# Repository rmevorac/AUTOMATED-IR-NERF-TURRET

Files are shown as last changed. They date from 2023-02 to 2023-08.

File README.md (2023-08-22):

# AUTOMATED IR NERF TURRET MECHA 20
# ME 405 Term Project

### by: Ben Elkayam, Ermias Yemane, Roey Mevorach

## Introduction
This projects goal was to design, construct and program a automated nerf turret that is capable of shooting a person 16 feet awya using an IR camera for signal detection. The firing conditions for this turret are a predetermined set of "dueling rules" specified in the following steps:

1. The turret must start facing away from the intended target
2. The turret will then roate 180 degrees to face the general area of the intended target
3. The intended target will have 5 seconds to move around. by this point your turret is allowed to fire.
4. After 5 seconds from the start of the duel the intended target must stand still for atleast 10 seconds.
5. The turret can fire any amount of shot sduring either step 3 or 4. The scoring is based on if the opposing targets turret hit first, how many shots hit, and how many shots missed. 

The turret is intended to be used exclusivley for the ME 405 Learn by Dueling Competition by the students who designed and programmed it and another other ME 405 students who wanted to try using the turret. 

---

# Turret Design

## Hardware Design
Our hardware design philisophy is based almost entirley around being compatible with the NERF gun we chose. For our turret we chose the NERF Ultra Select 2. An electronic firing mechanism and flywheel firing system where desirable as it made actuating the gun a pre-packaged operation. The only difficulty was the size of the gun made it difficult to design a fixture for. The design is outlined in [our CAD folder](https://github.com/rmevorac/ME-405-term-project/tree/main/SLDWRK). The 3 important design attributes of our final turret design are the yaw axis, the pitch axis, and the fixture. The yaw axis is composed of a lazy susan that sits on 4 legs conencting to the bottom half, and a pivot with a shaft coming through the middle of bearing downards which sits on the top. The yaw axis is driven by the 405 kot motors through a 400mm belt and a 3.75:1 torque pulley ratio. The pivot which composes the pitch axis as was designed around a set of 30mm bearing found within the ME 405 lab. The pivot piece which the large black 3D printed object, was printed with the assistance and guidance of Thomas Mcklay Taylor, another ME 405 student. The pitch axis is driven by a worm gear to spline gear system with an approximate gear ratio of 11:1 as to not be easily backdrivable. This drives a winch system that raises and lowers the gun. The pivot is attached to the final component set which is known as the gun clamp. This is a two piece mechanism which both acts as the shaft for which the gun pivots around and the mechanism which keeps the gun secured to the turret. Photos of the general design are provided below:

### General View:
<div align='center'>
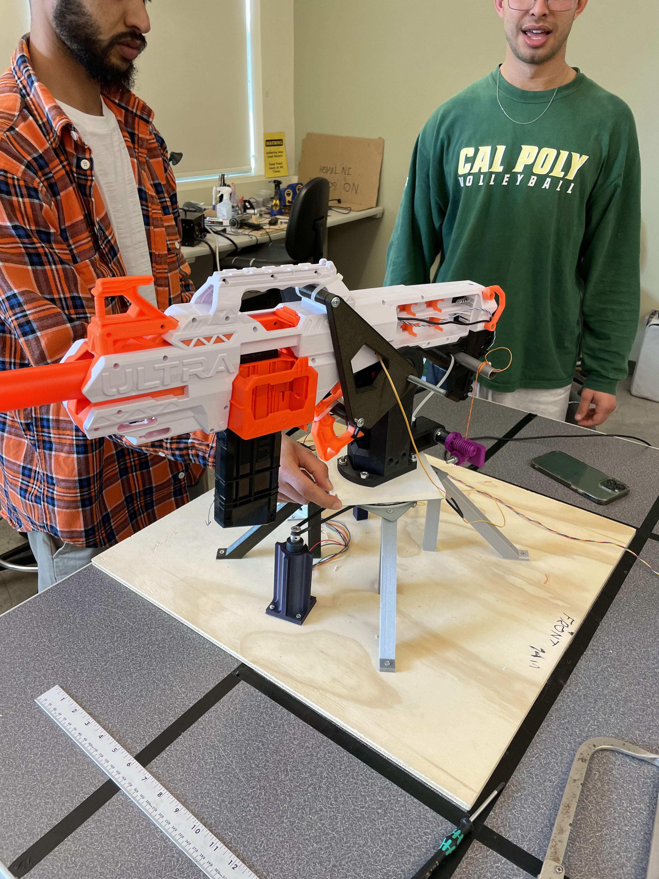
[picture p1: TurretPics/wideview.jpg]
wide view

</div>

### Yaw Axis:
<div align='center'>
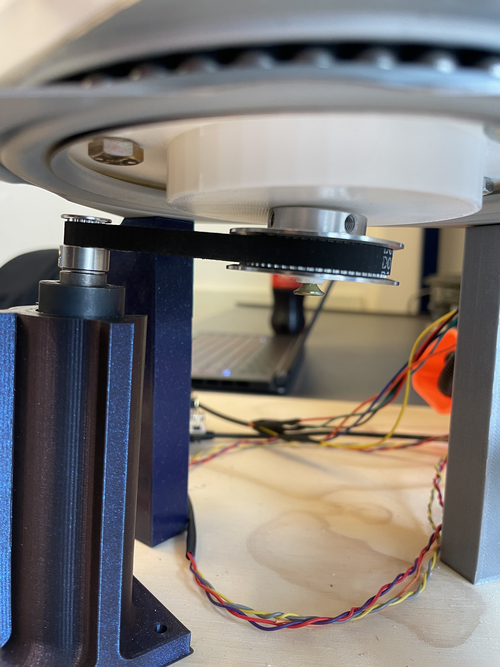
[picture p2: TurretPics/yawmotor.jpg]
yaw

</div>

### Pitch Axis:
<div align='center'>
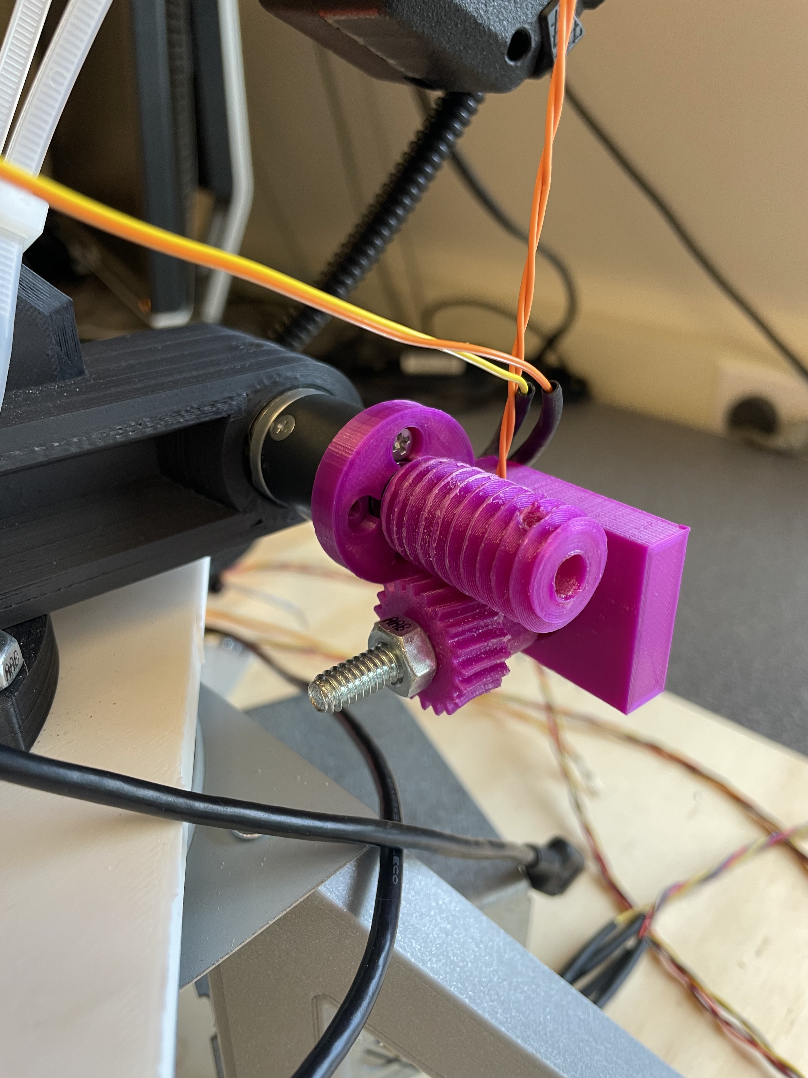
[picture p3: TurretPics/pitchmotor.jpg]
pitch

</div>

### Gun Pivot:
<div align='center'>
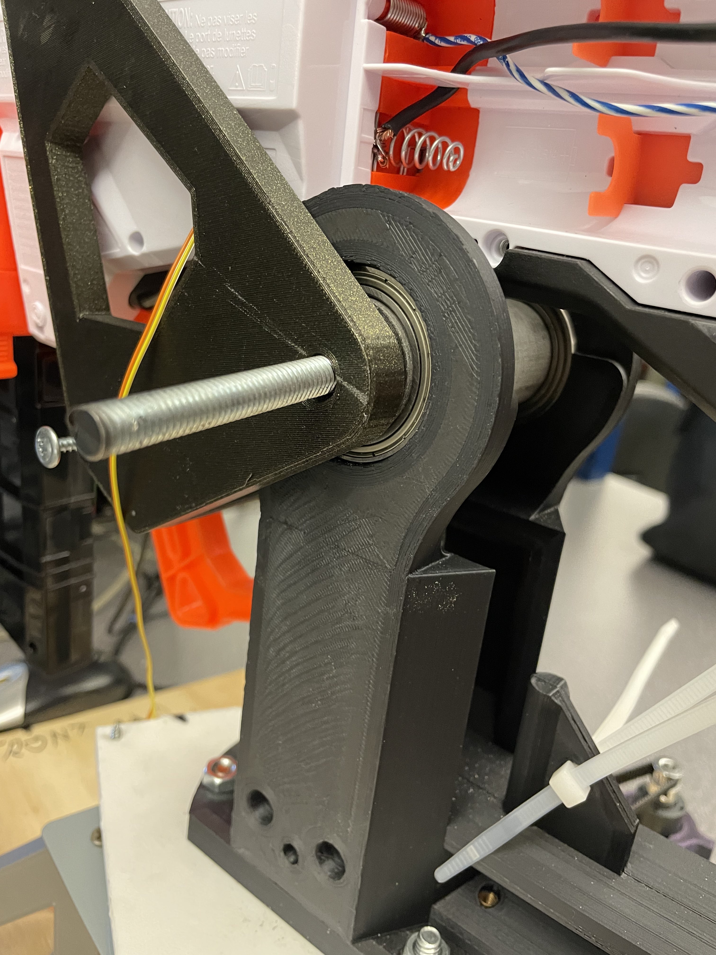
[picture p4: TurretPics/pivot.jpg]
pivot

</div>

### Firing Access Modification:
<div align='center'>
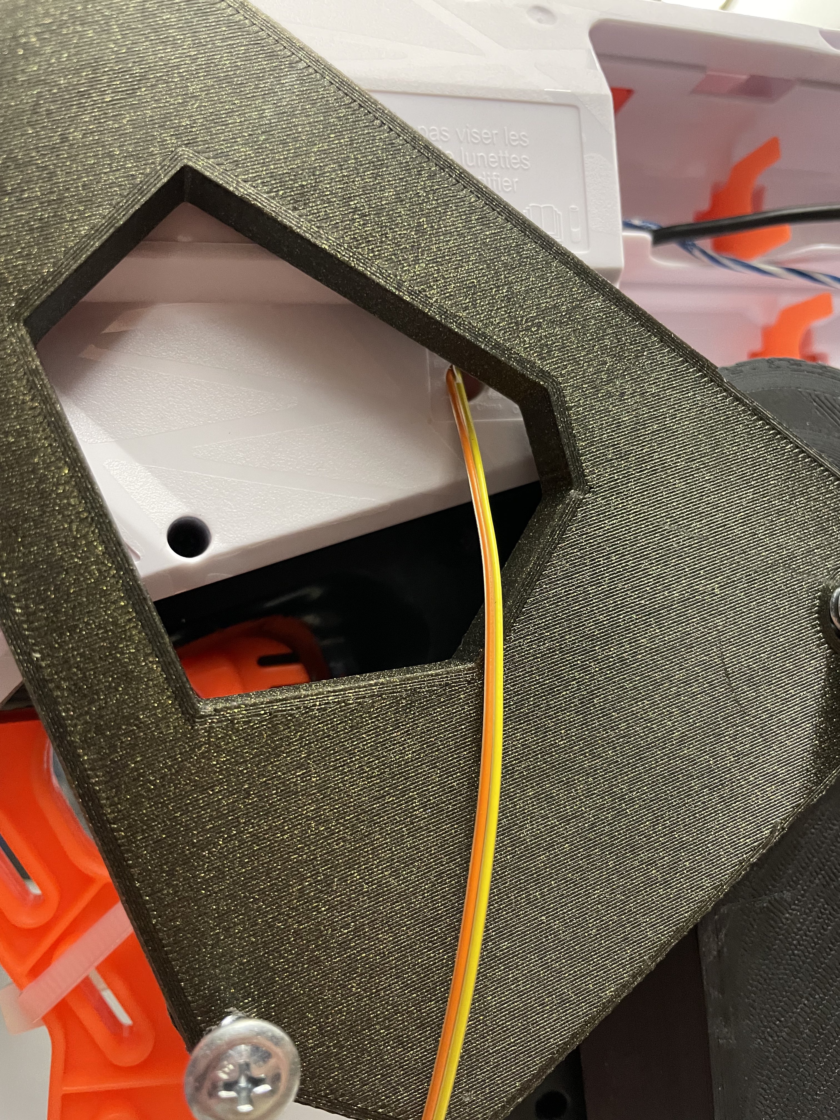
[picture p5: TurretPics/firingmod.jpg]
fireaccess

</div>

### Electronic Design
In terms of electronic design, the modifications made to the gun is directly replacing the firing signal from a button within the NERF gun with a set of wires to allow external control of the firing mechanism. The second change was to soder longer power cables to the battery touchpoints in order to have the turret be able to be connected to the power supplies. A secondary part of our electronic design is that we ziptied the flywheel trigger down rather than seek a direct electrical control solution because we realized we would always want the flywheels on.

## Software Design
Our software design is based on a cooperative multitasking design around 4 tasks. These tasks are our pitch motor, yaw motor, target acquisition, and firing mechanism.

Our code implements a cooperative multitasking scheduler using the cotask and task_share modules. Tasks are defined as functions, and they yield control back to the scheduler using the yield statement. The scheduler then runs the next task until it yields or completes. Shared data between tasks is managed using shared variables provided by the task_share module. Overall, the code is running several tasks concurrently and using shared variables to communicate between them, allowing for cooperative multitasking.

Our main program defines four tasks, two of which control the movement of the pitch and yaw motors. The program begins once the user button on the microcontroller is pressed. The system then begins its first task, which turns the gun around by 180 degrees. The system then waits for 5 seconds and moves to the next task. The next task uses the image produced by the IR camera to obtain the coordinates of the target (hottest pixel). These coordinates are then converted to ticks using simple geometry and other calculations, and are set as the motors' new setpoints. The motors then run until they reach the range of that setpoint. Once both motors are in position,
the final task is triggered, which fires the NERF gun.

Our Finite State diagrams and Task diagram are provided both here and in our doxygen. Our software design is provided in great detail on our doxygen gituhub.io page for this project, please refer to the link below for more detailed information: https://rmevorac.github.io/AUTOMATED-IR-NERF-TURRET/index.html

### Task Diagram:
<div align='center'>
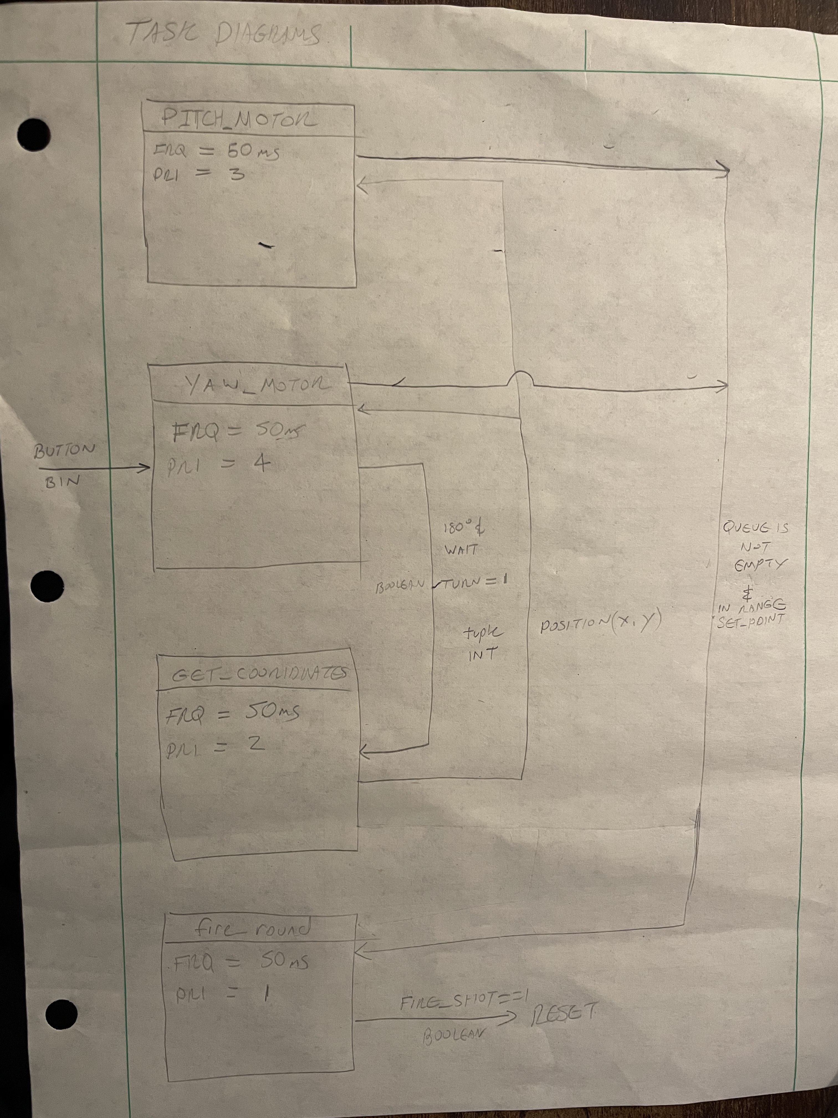
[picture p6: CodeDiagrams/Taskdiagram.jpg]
task

</div>

### Finite State Diagrams:
<div align='center'>
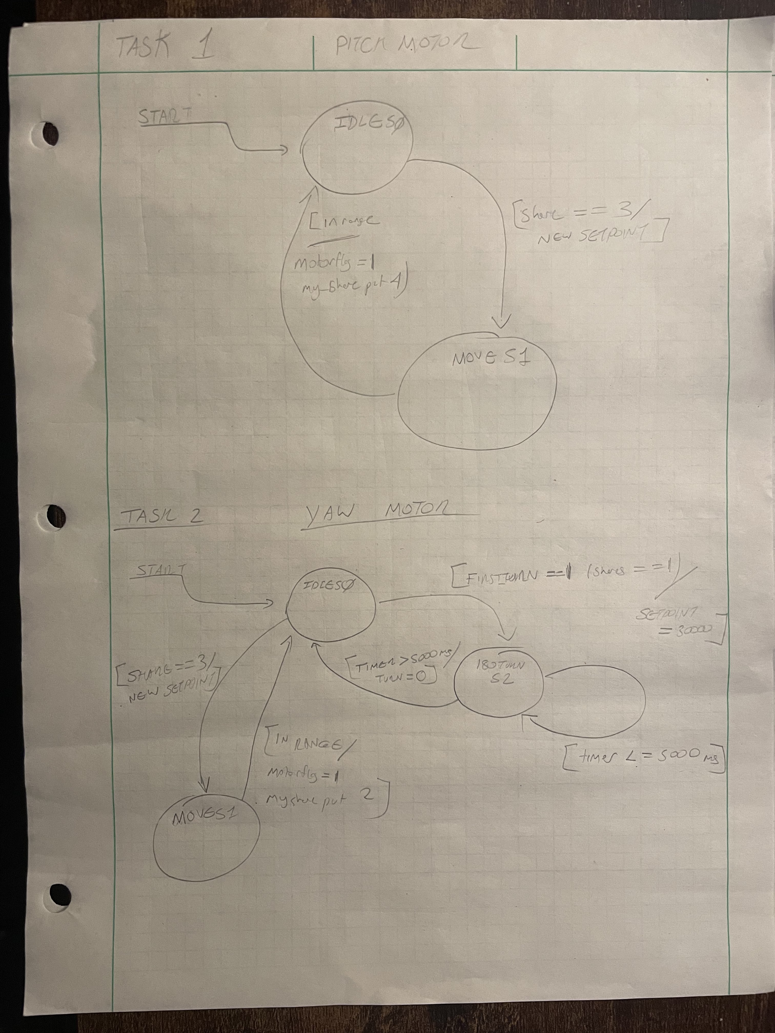
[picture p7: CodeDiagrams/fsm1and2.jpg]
fsm1and2
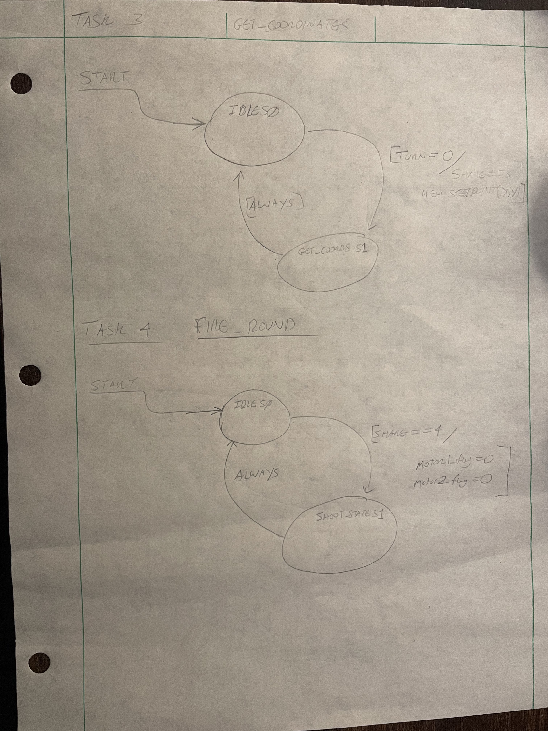
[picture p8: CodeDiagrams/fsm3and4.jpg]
fsm3and4
 
</div>

---

# Project Outcome

## Duel Day Performance
Our turret reach ours sections finals, but in a dissapointing way. Its tracking was excellent and was able to easily follow the target, however a mysterious code gremlin popped into our design sometime during the 3 hous between the end of our all-nighter the night before and our designated dueling time. While we lost no points, we gain none either as we could noot shoot. No amount of good tracking will fix a gun that doesnt shoot. We are unsure why it worked the night before then refused to work during the duel and did attempt to discover why during the friday after the duels. We eventually determined that the issue was a mixture of too much current draw and a strange calibration issue with our on/saftey stop button code. Ultimatley, we where proud of how our gun functioned while it worked and regret it could not operate at is best during the dueling day.

### Testing Results
We tested similarly to how we would duel, the onlly difference is that the test subject did not have their own turret at the end of the table. We decided to test like this because we wanted to calibrate the turrets accuracy to the same conditions the duel would take palce in. during the calibration testing the night before, the turret was opperating very effectivley and was landing 5 hits for every 8 shots. We anticiapted a good performance on duel day assuming the turret would function the same. 

## What We Learned
There was many things learned through this project and should be categorized into Mechanical, Eletrical and Software lessons. The brief summary for anyone attempting this project can be seen below in the Dos and Donts:

### Dos:
1.Use an eletrical firing system. Eletrical nerfguns are simply easier to actuate and shoot very effecitlvey. The pre-packaged design makes them easy to integrate into a turret.

2.Supply power through a power supply rather than batteries, we are grateful that it reduced the weight of our gun and during its functional peroid it gave us very consistent firing results.

3.Keep the tracking algorithim simple, we observed many people doing complex manipulation of the thermal array and have reduced accruacy than ours, just reading from the array keeps the processing light and provides highly reliable tracking.

4.Consider non-backdrivable systems. While the high gear ratio lsows down your turning, we removed alot of backlash in our axis that had our worm-spline gear system

5.We added a physical hardstop on our guns base to help us zero the gun for every duel. 

### Donts:
1. Do not rely on only 3D pritned components due to the fragility of them as tensile load bearing structures. Consider including wooden or metal components for this such as shafts.
2. Ensure that any custom eletric circuit system is as compatible as possible with the electronics within your NERF Gun as a lack of compatibility will cause misfires.
3. Conduct thorough tests to ensure new code does not inhibit core functions and prioritize that rather than calibration testing. 

### Mechanical Lessons
Most of our hardships where due to the heavy use of 3D printed parts. We originally designed our system to have pulleys fixed onto 3D printed shafts, however we soon realized why thats a problem. All our parts where experencing stress perpendicular to the plane of printing which caused layer seperation and broke our shafts and bearing mounts off. This was remedied in two ways. The layer seperation on our bearing mounts was fixed with the help of Thomas Taylor who advised on a printing strategy that would change the direction of the print layer and increase strucutral rigidity through brass inserts. We are very grateful for his assistance concerning this part and his advice has helped all of us become more competent designers for 3D printing. For the shafts, thier snapping was remedied differently depending on the axis. For the yaw shaft, a generous amount of plastic bonder cement was applied with the snapped shaft and pulley to the original base. For the pitch shaft, the system was replaced with the worm gear-spline gear winch mechanism which opperated with much less backlash than the original pulley system. Overall the lesson here is do not trust 3D printing on its own for structural applications, it should be combined with additional components and be put in compression rather than tensile loads.

### Eletrical Lessons
The eletrical side of our turret seemed to work fine up until our last moments, wherein we suspect it to possibly be part of our firing issue. The turret's firing mechanism is a simple circuit with the two firing wires sending a shoot signal when shorted. To protect the STM output pins, we implemented a BJT-transistor switch which was used to open and close the connection. This was the extent of the circuit we had, which leads us to believe that we possibly needed to investigate our eletrical circuit much more thoroughly to ensure we would not have misfires as one of our members believes that current leakage may of been our issue or that our microcontroller could not provide enough current because the gate capacitance was too large.

### Software Lessons

Our software side learning was the most mild as all the previous tools such as our motor controller and camera components where easy to implement. We decided to go with a simple but effective scanning method with our camera wherein we simply checked every cell and its neighbors. The cell with the highest combined value of itself and its neighbors had its row and column stored and we did that for the entire thermal camera array. This system provided us good tracking results after some calibration. Our biggest coding hump was trying to implement a system that allowed us to use the blue user button on the microcontroller to start and stop the turret. We first where having issues with our ExtInt system throwing errors which was due to improper naming conventions within our code and then had trouble implmenting it into our code. We ended up putting each of our tasks in a while loop that depended on the button's boolean being set in order to function, this gave use essentially a pause button functionality on our turret.

---

# Original Description and additional files

We are intending to make a 2 axis turret equipped with an electronic nerf launcher. The goal is to use a medium sized motor likely one of the tub motors for horizontal panning and either a more powerful motor we purchased online or a dual tub motor gearbox. We are likely going to 3D print most of the superstructural pieces and manufacture components like the trigger mechanism. The goal is to get the gun to land the first shot. We are confident on our electric gun choice but unsure on the motor selection.

Motors: 
Pitch Motor : Tub motor 
Yaw Motor: 1 – 2 Tub motors

Drive System: 
Pitch: Likely a single gear step (not including gearbox on motors) in the range of 2:1 to 4:1
Yaw: Also a single gear step in the range of 2:1 to 5:1 or utilize a two motor gearbox

Nerf Gun:
Vendor: Amazon
Model: Nerf Ultra Select
https://www.amazon.com/NERF-F0958-NER-Ultra-Select/dp/B08SYD2685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

Data sheet for Nerf Gun: https://icecat.biz/p/nerf/f0958u50/ultra-toy+weapons-5010993855285-select-89523906.html

Data sheet for Adafruit MLX90640 IR Thermal Camera: https://learn.adafruit.com/adafruit-mlx90640-ir-thermal-camera/downloads

Trigger System:
Electronic Trigger System

Total Cost:
Nerf Ultra Select Gun - $51

Task Diagram:
<div align='center'>
TDV1
</div>

FSM:
<div align='center'>
FSMV1
</div>

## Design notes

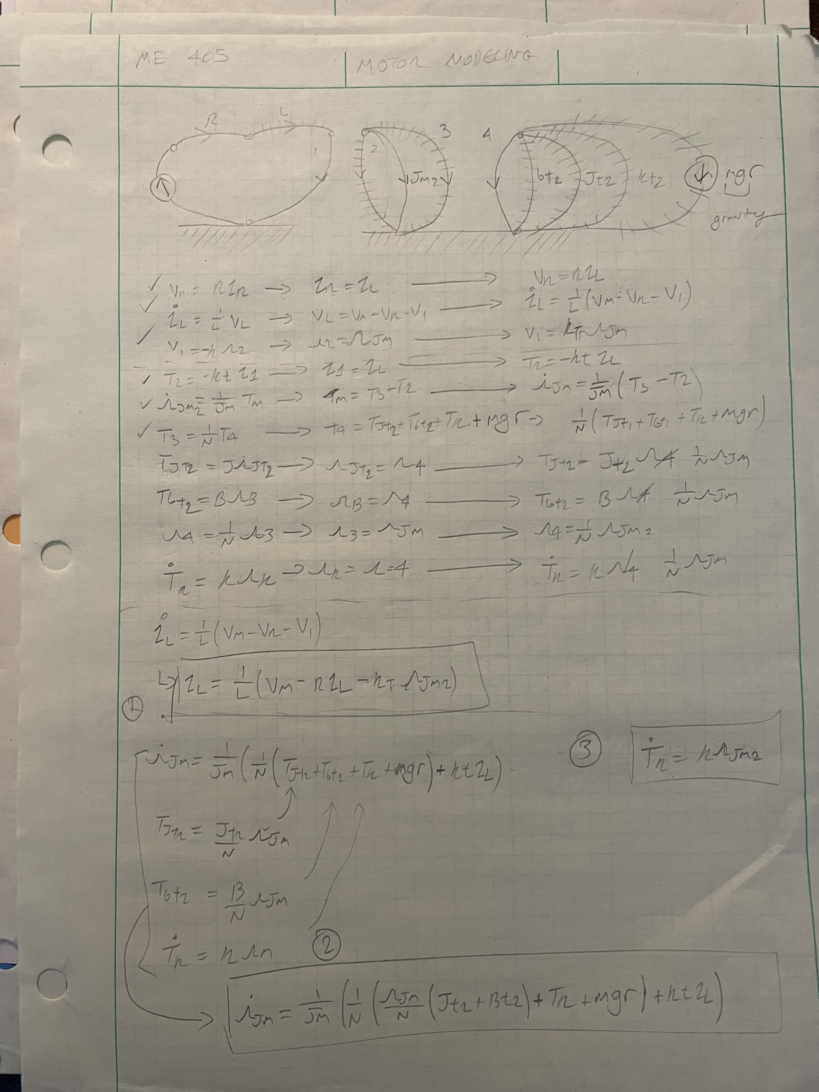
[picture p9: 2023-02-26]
spec_docs/equations/motor2_img1.jpg

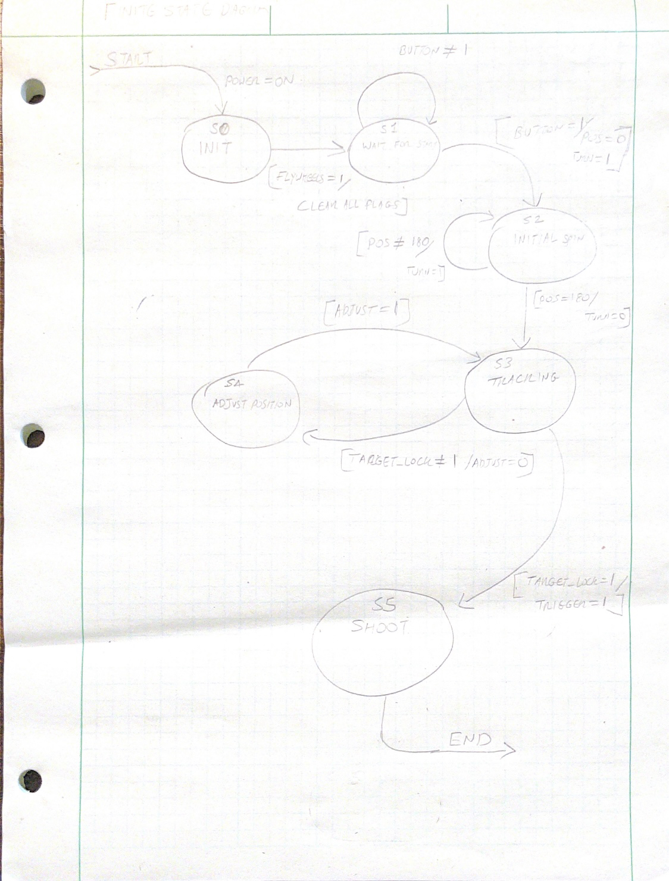
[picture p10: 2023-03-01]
spec_docs/FSMV1.jpg

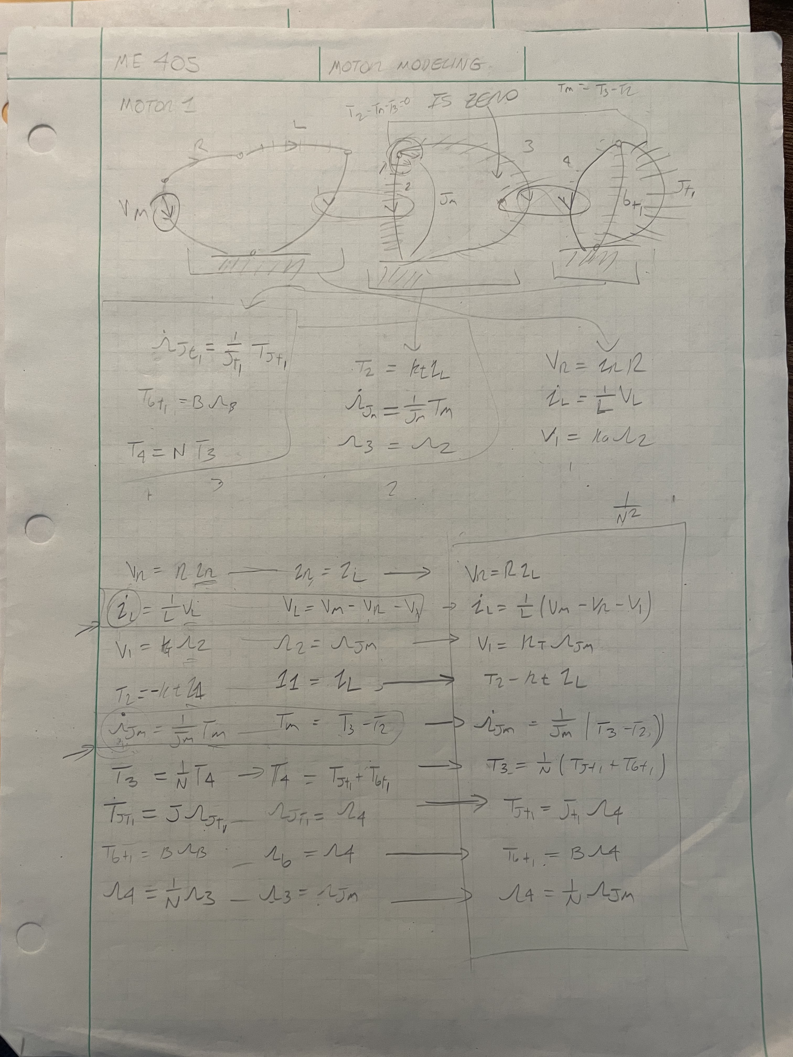
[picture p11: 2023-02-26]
spec_docs/equations/motor1_img1.jpg

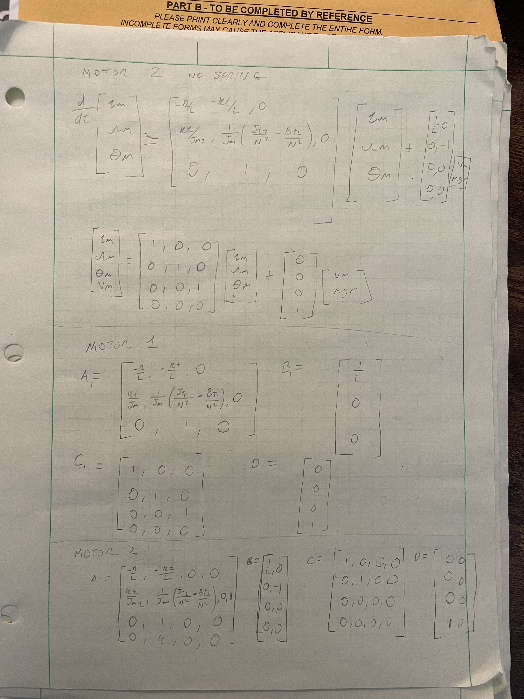
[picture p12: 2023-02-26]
spec_docs/equations/matrices_without_spring.jpg

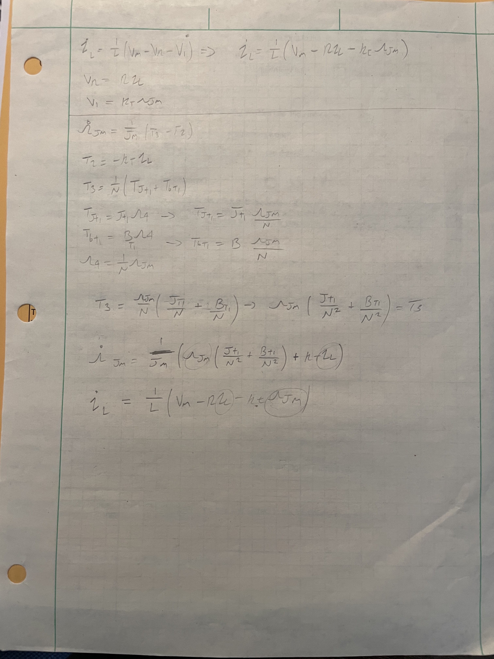
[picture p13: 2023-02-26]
spec_docs/equations/motor1_img2.jpg

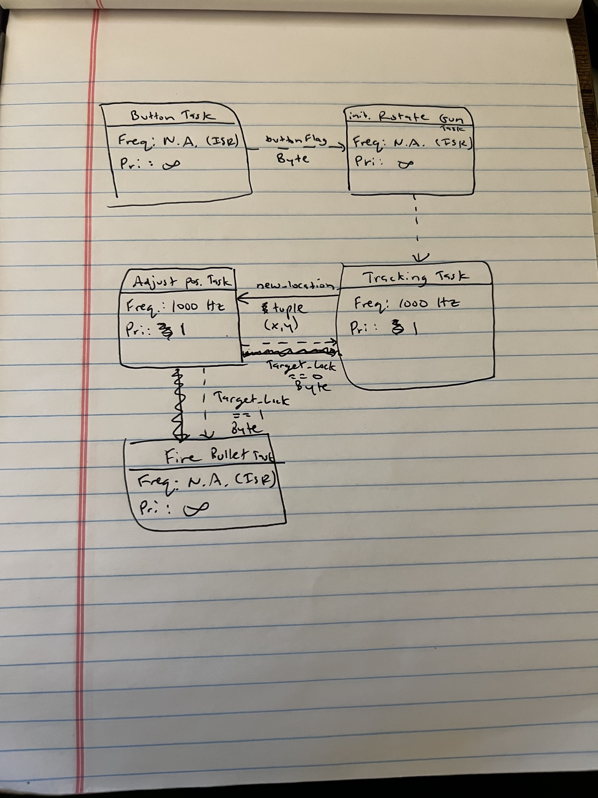
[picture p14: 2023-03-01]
spec_docs/TDV1.jpg

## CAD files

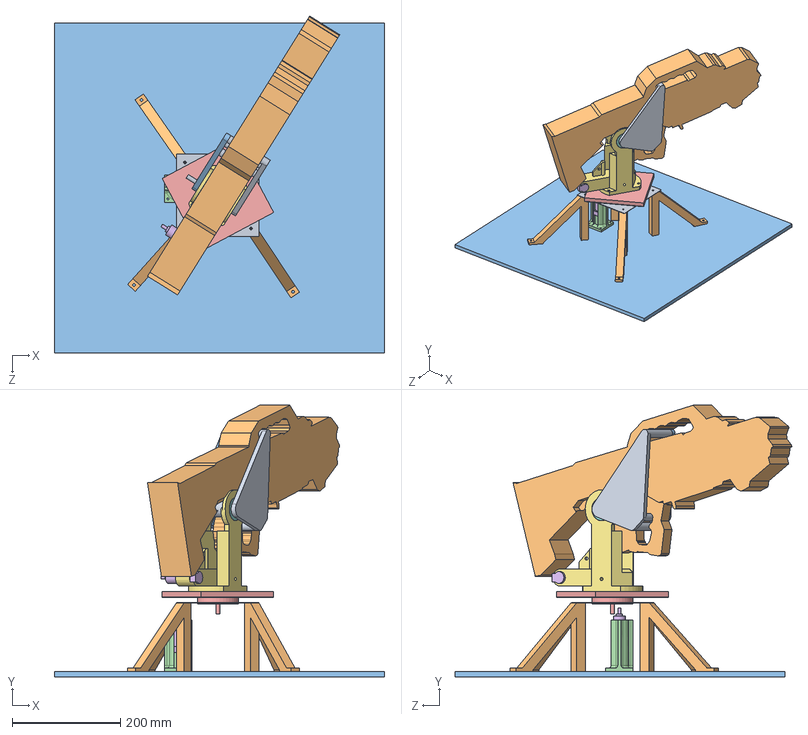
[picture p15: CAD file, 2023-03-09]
SLDWRK/Mainassemb.SLDASM
609.6 x 501.6 x 622.5 mm
LSB
base legs x 4
baseboard
LST
3d topbase
verticalframe
bearings x 2
clamp1
gun
clamp2
motormountyaw

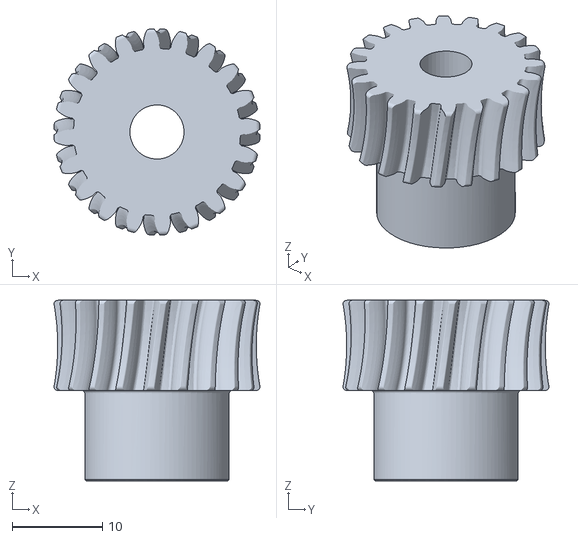
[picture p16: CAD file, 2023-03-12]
SLDWRK/Part1.STL
22.8 x 22.8 x 20.0

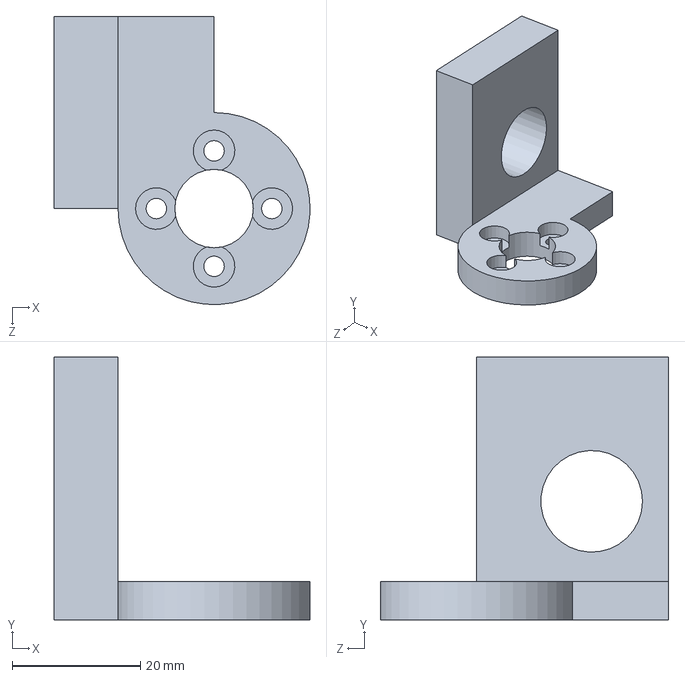
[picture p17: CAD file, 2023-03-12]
SLDWRK/winchmount.SLDPRT
40.0 x 41.0 x 45.0 mm

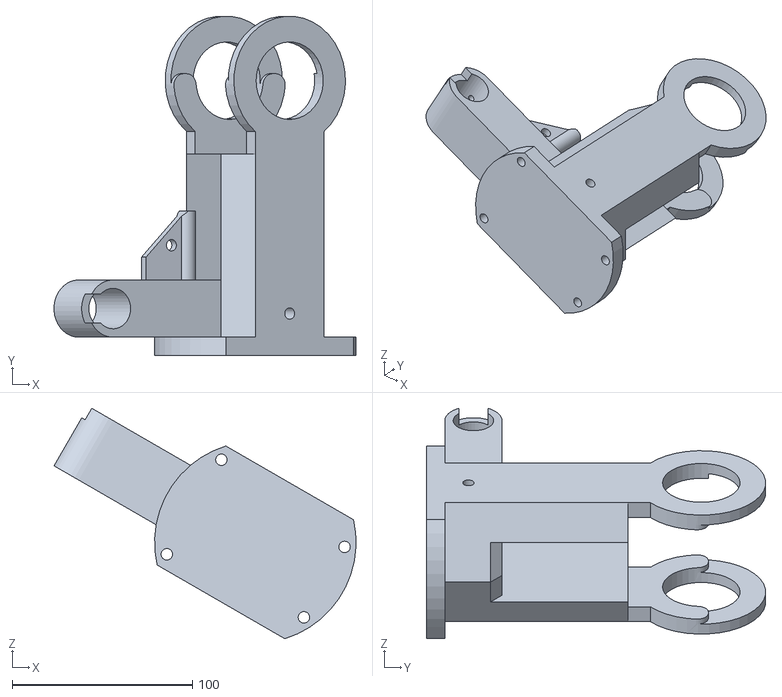
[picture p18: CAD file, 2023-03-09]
SLDWRK/verticalframeversion2.STL
167.5 x 188.0 x 127.8

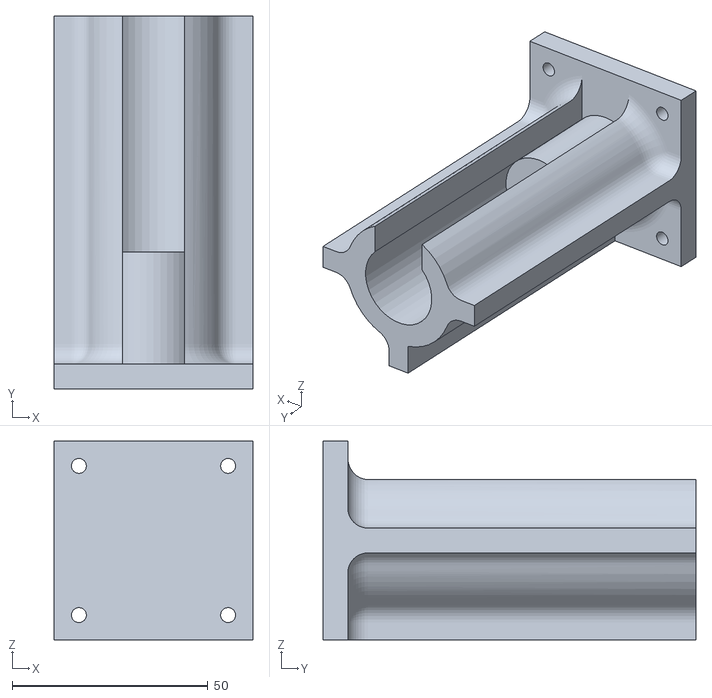
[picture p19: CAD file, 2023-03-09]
SLDWRK/motormountyaw.STL
50.8 x 95.2 x 50.8

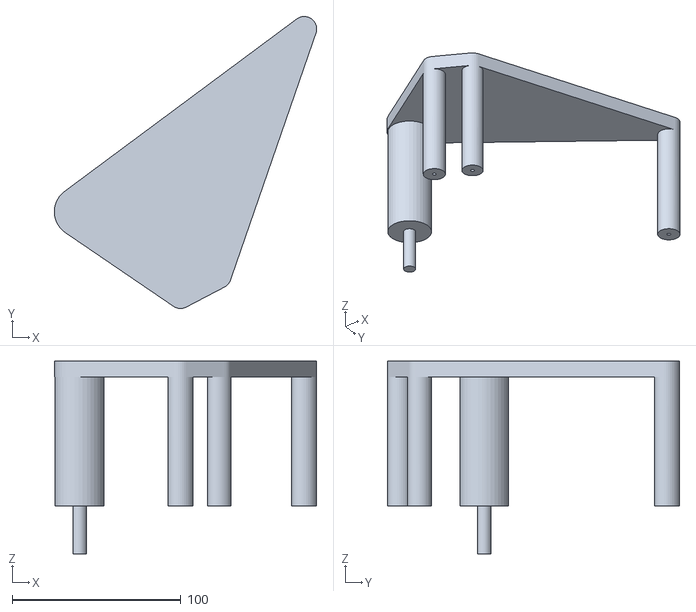
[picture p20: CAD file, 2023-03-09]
SLDWRK/clamp1.STL
155.6 x 173.1 x 114.4

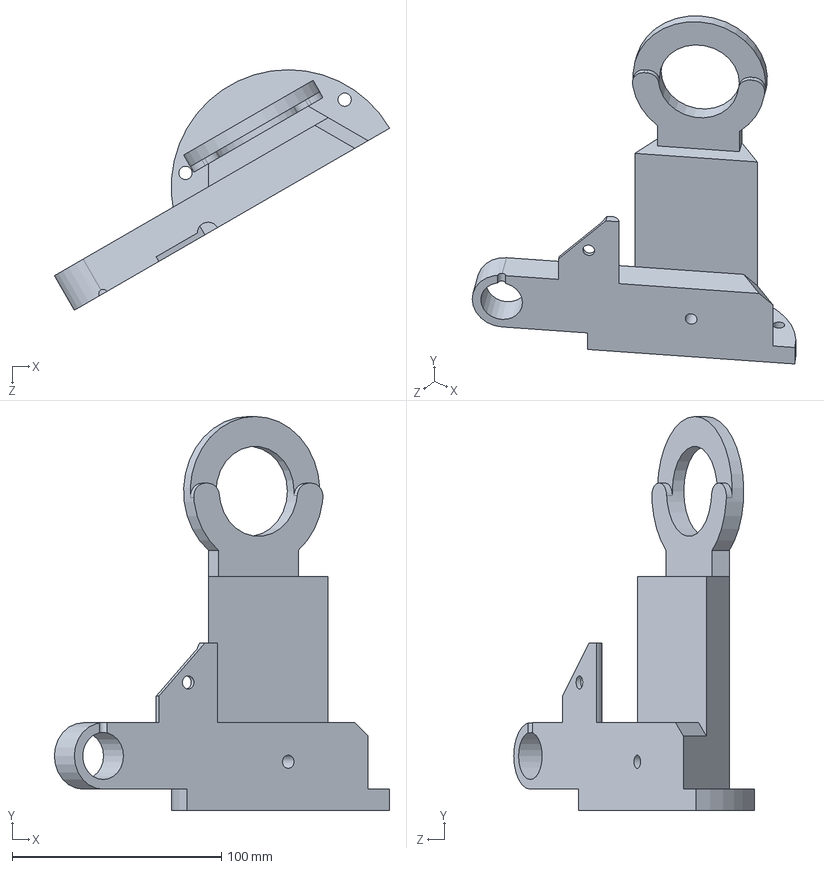
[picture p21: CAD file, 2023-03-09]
SLDWRK/verticalframesplit1.SLDPRT
160.1 x 188.1 x 114.9 mm

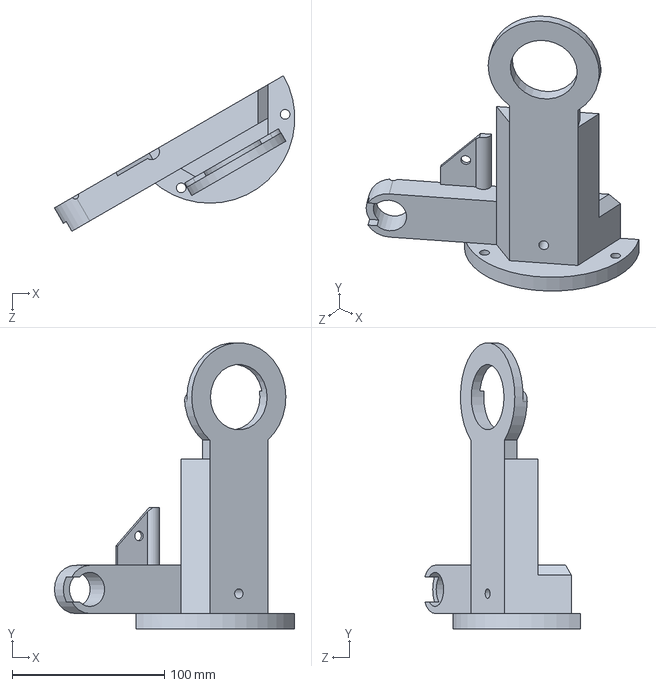
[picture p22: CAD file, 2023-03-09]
SLDWRK/verticalframesplit2.SLDPRT
157.9 x 188.0 x 102.3 mm

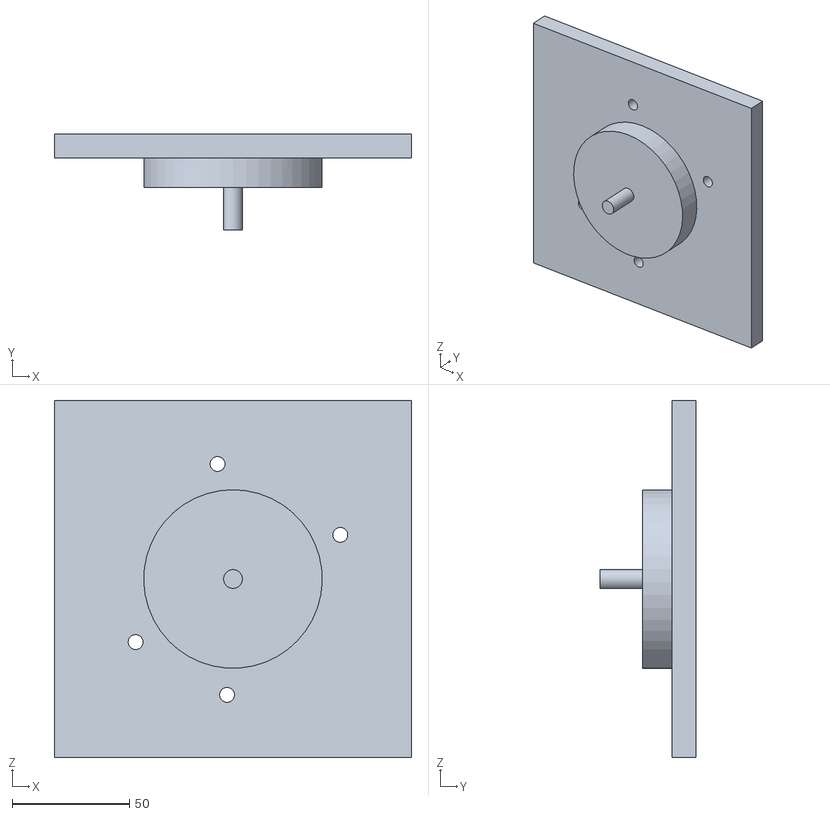
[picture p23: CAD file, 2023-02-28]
SLDWRK/3d topbaseV2.STL
152.4 x 40.9 x 152.4

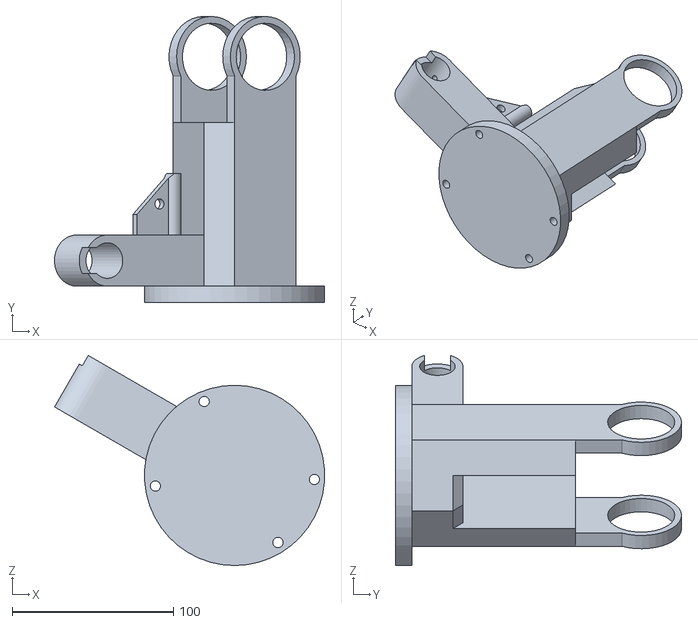
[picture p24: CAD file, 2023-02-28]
SLDWRK/verticalframeSTRUCTURE.STL
167.4 x 177.4 x 130.2

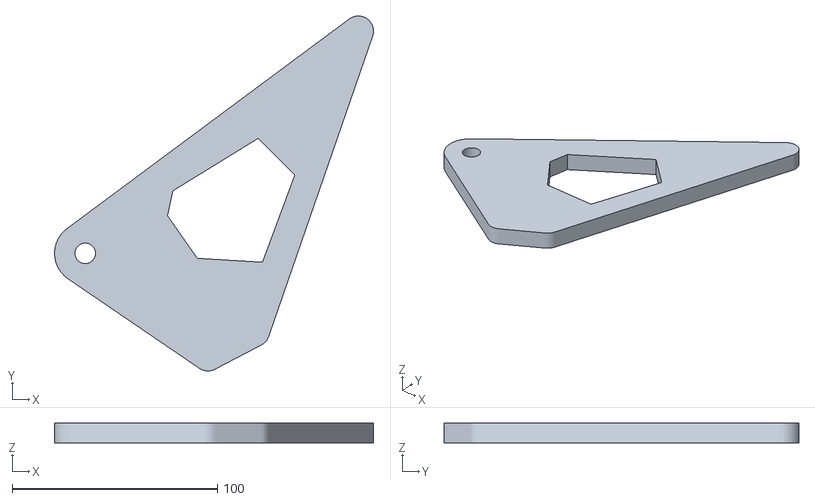
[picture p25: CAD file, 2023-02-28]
SLDWRK/clamp2.STL
155.6 x 173.1 x 9.53

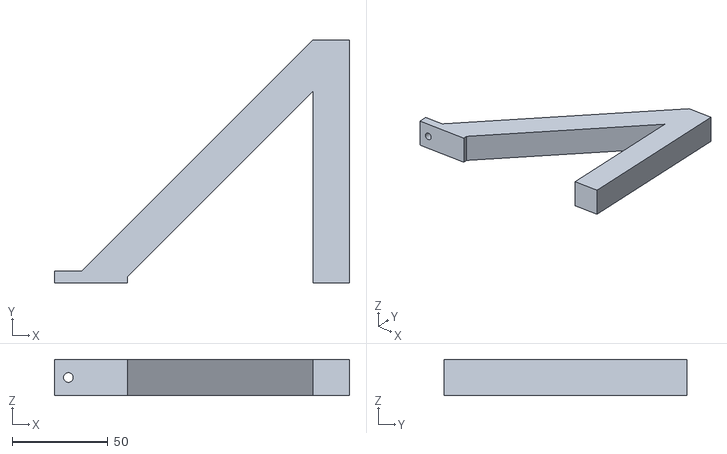
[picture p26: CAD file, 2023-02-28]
SLDWRK/base legs.STL
154.0 x 127.0 x 19.1

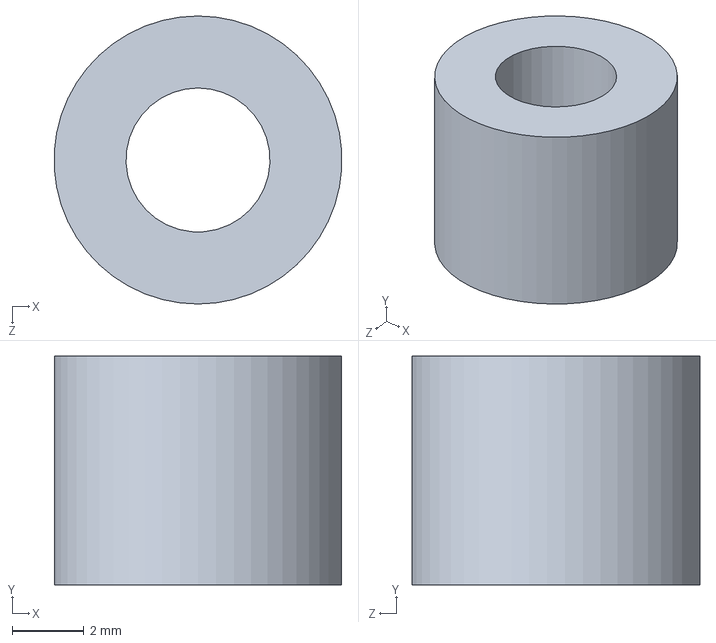
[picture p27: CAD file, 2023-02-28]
SLDWRK/8to6shim.SLDPRT
7.98 x 6.35 x 8.00 mm

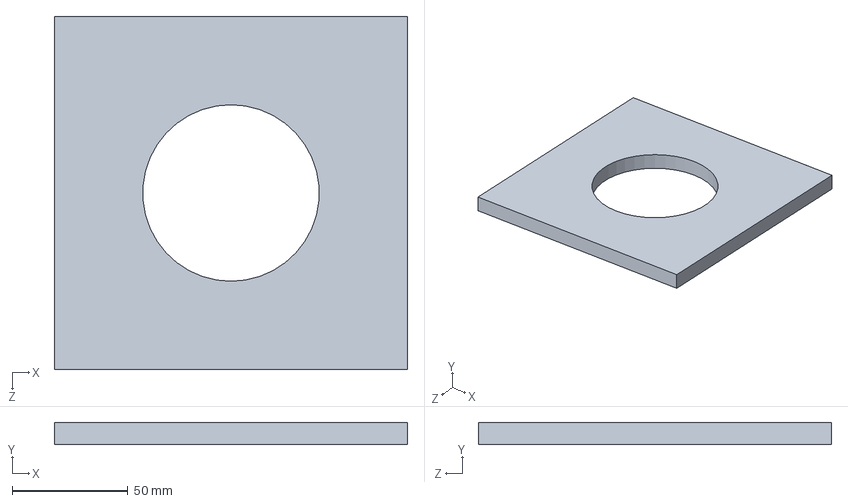
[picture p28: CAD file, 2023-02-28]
SLDWRK/plywood topbase.SLDPRT
152.4 x 9.53 x 152.4 mm

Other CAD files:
SLDWRK/3d topbase.SLDPRT
SLDWRK/57545K764_Metal Worm Gear.SLDPRT
SLDWRK/57545K633_Steel Worm.SLDPRT
SLDWRK/3d topbase.STL
SLDWRK/57545K633_Steel Worm.STL
SLDWRK/57545K764_Metal Worm Gear.STL
SLDWRK/verticalframesplit1.STL
SLDWRK/verticalframesplit2.STL
SLDWRK/winchmount.STL

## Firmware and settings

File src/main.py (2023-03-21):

"""!
@file main.py
    This code is for a control system that moves a NERF gun to a specific set of angles using
    two motors: a pitch and yaw motor. The system includes a IR camera (MLX90640), which produces
    an image to obtain the coordinates of the target. The system is activated/paused by pressing
    the user button on the microcontroller.

    This program implements a cooperative multitasking scheduler using the cotask and task_share modules.
    Tasks are defined as functions, and they yield control back to the scheduler using the yield statement.
    The scheduler then runs the next task until it yields or completes. Shared data between tasks is
    managed using shared variables provided by the task_share module. Overall, the code is running several
    tasks concurrently and using shared variables to communicate between them, allowing for cooperative multitasking.

    This program defines four tasks, two of which control the movement of the pitch and yaw motors. The program
    begins once the user button on the microcontroller is pressed. The system then begins its first task, which
    turns the gun around by 180 degrees. The system then waits for 5 seconds and moves to the next task. The next task
    uses the image produced by the IR camera to obtain the coordinates of the target (hottest pixel). These
    coordinates are then converted to ticks using simple geometry and other calculations, and are set as the motors'
    new setpoints. The motors then run until they reach the range of that setpoint. Once both motors are in position,
    the final task is triggered, which fires the NERF gun.


@author Ben Elkayam
@author Roey Mevorach
@author Ermias Yemane

@date   2023-Mar-20
"""
"""!
@package pyb                Contains all micro controller tools we use.
@package gc                 Contains a garbage collector tool.
@package utime              Contains functions for getting the current time and date, measuring
                            time intervals, and for delays.
@package machine            Contains specific functions related to the hardware on a particular board.
@package math               Contains mathematical functions.

@package cotask             Contains the class to run cooperatively scheduled tasks in amultitasking system.
@package task_share         Contains the class that allows tasks to share data without the risk
                            of data corruption by interrupts.
@package encoder_reader     Contains our encoder driver class and data.
@package motor_driver       Contains our motor driver class that interfaces with the encoder.
@package controller         Contains our controller class which combines the motor and encode classes.
@package mlx_cam            Contains a wrapper class for accessing and using the IR camera (MLX90640)
"""
import pyb
import gc
import utime as time
from machine import Pin, I2C
from math import atan, pi

import task.cotask as cotask
import task.task_share as task_share
from motor.encoder_reader import Encoder
from motor.motor_driver import MotorDriver
from motor.controller import Controller
from mlx90640.mlx_cam import MLX_Cam

NUM_PIXELS_COL = 32
NUM_PIXELS_ROW = 24

def button_press(pin):
    """!
    @brief      This is the callback function that is called when the interrupt
                is triggered when the user button is pressed
    @details    This function is called when the user button on the microcontroller
                is pressed. The global variable button_count starts at 0. It is then
                incremented to 1 when the button is pressed for the first time, allowing
                the program to run. When the button is pressed again, button_count is
                then decremented back to zero, which halts the program.
    @param      pin The pin on which to enable the interrupt
    @return     None
    """
    try:
        print("button pressed")
        global button_count

        if button_count:
            button_count -= 1
        else:
            button_count += 1

    except:
        pass

def move_pitch_motor(shares):
    """!
    @brief      This task moves the pitch motor until it reaches its setpoint.
    @details    This task has 2 states: IDLE (S0) and MOVING (S1). When this task is
                in S0, the pitch motor is idle. When this task is in S1, the pitch
                motor continuously runs and checks its position against its setpoint.
                When the position is within 10000 ticks of its setpoint, it checks
                if the yaw motor has reached its position. If my_queue has any items
                in it, then the yaw motor has reached its position and the system 
                transitions to the next task (firing a shot).
    @param      shares A tuple of two shares, one for `my_share` and one for `my_queue`.
    @return     None
    """
    # Get references to the share and queue which have been passed to this task
    my_share, my_queue = shares

    while 1:
        if my_share.get() == 3: # MOVE STATE (S1)
            while 1:
                controller1.run()
#                 print(f"p_p: {controller1.encoder.position}, sp_p: {controller1.setpoint}")

                if controller1.encoder.position in\
                 range(controller1.setpoint - 10000, controller1.setpoint + 10000):
                    print("reached pitch")
                    if my_queue.any():
                        my_share.put(4)
                        break
                yield
            yield
        else: # IDLE STATE (S0)
            yield

def move_yaw_motor(shares):
    """!
    @brief      This task moves the yaw motor until it reaches its setpoint.
    @details    This task has 3 states: IDLE (S0), MOVING (S1), and 180 TURN (S2).
                When this task is in S0, the yaw motor is idle. When this task is
                in S1, the yaw motor continuously runs and checks its position
                against its setpoint. When the position is within 100 ticks of its
                setpoint, it puts 1 in my_queue, which lets the pitch motor know that
                it has reached its position. When this task is in S2, a timer
                starts and then the yaw motor runs until it has completed a 180 deg
                turn. Once 5 seconds have past, the system transitions to the next task
                (getting the coordinates for the hotspot from the IR Cam input)
    @param      shares A tuple of two shares, one for `my_share` and one for `my_queue`.
    @return     None
    """
    # Get references to the share and queue which have been passed to this task
    my_share, my_queue = shares

    while 1:
        if my_share.get() == 3: # MOVE STATE (S1)
            while 1:
                controller2.run()
#                 print(f"p_y: {controller2.encoder.position}, sp_y: {controller2.setpoint}")

                if controller2.encoder.position in\
                 range(controller2.setpoint - 100, controller2.setpoint + 100):
                    print("reached yaw")
                    if not my_queue.any():
                        my_queue.put(1)
                    break
                yield
            yield
        elif my_share.get() == 1: # 180 TURN STATE (S2)
            ## Start timer
            timer = time.ticks_ms()
            while 1:
                controller2.run()
                # Completes 180 deg turn
                if controller2.encoder.position in range(29650, 30350):
#                     print(f"timer = {timer}, {time.ticks_ms()}")
                    if time.ticks_diff(time.ticks_ms(), timer) >= 5000:
                        print("done with delay")
                        controller2.encoder.zero()
                        motor2.set_duty_cycle(0)
                        my_share.put(2)
                        break
                yield
            yield
        else: # IDLE STATE (S0)
            yield

def get_coordinates(shares):
    """!
    @brief      Get the coordinates of the maximum value in the camera image.
    @details    This task has 2 states: IDLE (S0) and GET COORDINATES (S1).
                When this task is in S0, the task does nothing. When this task
                is in S1, this task retrieves the camera image, processes it, and calculates
                the coordinates of the pixel with the maximum value. It then converts
                these coordinates to distance and ticks, and sends them to the pitch and yaw
                motor controllers. Once those values are sent, the transitions to the
                next task (move motors).
    @param      shares A tuple of two shares, one for `my_share` and one for `my_queue`.
    @return     None
    """
    # Get references to the share and queue which have been passed to this task
    my_share, my_queue = shares

    while 1:
        if my_share.get() == 2: # GET COORDINATES STATE (S1)
            max_val, max_row, max_col = 0, 0, 0
            row, col = 1, 1

            image = camera.get_image()
#             camera.ascii_image(image.pix)
            pix = camera.get_csv(image.pix, limits=(0, 99))
            next(pix)
        #     print(f"MAX: {max_val}")

            while row < (NUM_PIXELS_ROW - 2):
        #         print(f"MAX: {max_val}") 
                line = next(pix).split(",")
        #         print(line)
                while col < (NUM_PIXELS_COL - 1):
                    if int(line[col]) > max_val:
                        avg = (int(line[col - 1]) + int(line[col]) + int(line[col + 1])) / 3
                        if avg > max_val:
#                             print(f"updated at {row}, {col} to value {avg}")
                            max_val = avg
                            max_row = row
                            max_col = col
                    col += 1
                row += 1
                col = 1
#             print(f"val: {max_val}, row: {max_row}, col: {max_col}")

            x_dist = (16 - max_col) * 2.8
            y_dist = (12 - max_row) * 3.7
#             print(f"x_dist: {x_dist}, y_dist: {y_dist}")
            
            x_ticks = int((atan(x_dist/180) * 60000) // (2 * pi)) + 320
            y_ticks = int((atan(y_dist/180) * 528000) // (2 * pi))
            
#             print(f"x: {x_ticks}, y: {y_ticks}")
            controller1.encoder.zero()
            controller2.encoder.zero()
            controller1.set_setpoint(y_ticks)
            controller2.set_setpoint(x_ticks)
            my_share.put(3)
            yield
        else: # IDLE STATE (S0)
            yield

def fire_round(shares):
    """!
    @brief      Get the coordinates of the maximum value in the camera image.
    @details    This task has 2 states: IDLE (S0) and GET COORDINATES (S1).
                When this task is in S0, the task does nothing. When this task
                is in S1, this task initiates the shooting procedure by setting
                the logic level of the trig_pin to high for 500 ms. This is the
                time it takes for the gun to fire one shot. This task then turns
                off the motors and transitions the system to the an idle state.
    @param      shares A tuple of two shares, one for `my_share` and one for `my_queue`.
    @return     None
    """
    # Get references to the share and queue which have been passed to this task
    my_share, my_queue = shares

    while 1:
        if my_share.get() == 4: # SHOOT STATE (S1)
            trig_pin.value(1)
            pyb.delay(500)
            trig_pin.value(0)
            print("bang")
            motor1.set_duty_cycle(0)
#             print("motor 1 shut off")
            motor2.set_duty_cycle(0)
#             print("motor 2 shut off")
            my_queue.clear()
            my_share.put(0)
            yield
        else: # IDLE STATE (S0)
            yield


if __name__ == "__main__":
    ## Set kp and setpoints for controllers 1 (pitch) where kp = 1 and setpoint = 0
    kp1, sp1 = 1, 0

    ## Set kp and setpoints for controllers 2 (yaw) where kp = 1 and setpoint = 32000 (180 deg turn)
    kp2, sp2 = 1.5, 30000
    
    ## Create pin for trigger fire
    trig_pin = Pin(Pin.board.PA4, Pin.OUT_PP)

    ## Create a share to test function and diagnostic printouts
    share0 = task_share.Share('h', thread_protect=False, name="Share 0")

    ## Create a queue to test function and diagnostic printouts
    q0 = task_share.Queue('h', 16, thread_protect=False, overwrite=False,
                          name="Queue 0")

    # The following import is only used to check if we have an STM32 board such
    # as a Pyboard or Nucleo; if not, use a different library
    try:
        from pyb import info

    # Oops, it's not an STM32; assume generic machine.I2C for ESP32 and others
    except ImportError:
        # For ESP32 38-pin cheapo board from NodeMCU, KeeYees, etc.
        i2c_bus = I2C(1, scl=Pin(22), sda=Pin(21))

    # OK, we do have an STM32, so just use the default pin assignments for I2C1
    else:
        i2c_bus = I2C(1)

    ## Select MLX90640 camera I2C address, normally 0x33, and check the bus
    i2c_address = 0x33
    scanhex = [f"0x{addr:X}" for addr in i2c_bus.scan()]
#     print(f"I2C Scan: {scanhex}")

    ## Create the camera object and set it up in default mode
    camera = MLX_Cam(i2c_bus)

    ## Create motor 1 object (pitch)
    motor1 = MotorDriver(Pin.board.PC1, Pin.board.PA0, Pin.board.PA1, 5)
    motor1.set_duty_cycle(0)

    ## Create motor 2 object (yaw)
    motor2 = MotorDriver(Pin.board.PA10, Pin.board.PB4, Pin.board.PB5, 3)
    motor2.set_duty_cycle(0)

    ## Create encoder 1 object (pitch)
    encoder1 = Encoder(Pin.board.PC6, Pin.board.PC7, 8)
    
    ## Create encoder 2 object (yaw)
    encoder2 = Encoder(Pin.board.PB6, Pin.board.PB7, 4)

    ## Once motor, encoder and params are collected they are used to create this controller 1 object (pitch)
    controller1 = Controller(kp1, sp1, motor1, encoder1)

    ## Once motor, encoder and params are collected they are used to create this controller 2 object (yaw)
    controller2 = Controller(kp2, sp2, motor2, encoder2)

    ## Initialize button_count to turn microcontroller on/off
    global button_count

    ## Set button_count to 0 (off)
    button_count = 0

    ## Set up the interrupt pin for when a button is pressed. Pressing the button starts/stops the system
    button_pin = pyb.ExtInt(Pin.board.PC13, pyb.ExtInt.IRQ_FALLING, Pin.PULL_UP, button_press)


    # Create the tasks. If trace is enabled for any task, memory will be
    # allocated for state transition tracing, and the application will run out
    # of memory after a while and quit. Therefore, use tracing only for 
    # debugging and set trace to False when it's not needed
    task1 = cotask.Task(move_pitch_motor, name="Task_1", priority=3, period=50,
                        profile=True, trace=False, shares=(share0, q0))
    task2 = cotask.Task(move_yaw_motor, name="Task_2", priority=4, period=50,
                        profile=True, trace=False, shares=(share0, q0))
    task3 = cotask.Task(get_coordinates, name="Task_3", priority=2, period=50,
                        profile=True, trace=False, shares=(share0, q0))
    task4 = cotask.Task(fire_round, name="Task_4", priority=1, period=50,
                        profile=True, trace=False, shares=(share0, q0))
    cotask.task_list.append(task1)
    cotask.task_list.append(task2)
    cotask.task_list.append(task3)
    cotask.task_list.append(task4)
    
    # Put state number into shares. Initialized to state 1
    share0.put(1)

    # Run the memory garbage collector to ensure memory is as defragmented as
    # possible before the real-time scheduler is started
    gc.collect()

    # Run the scheduler with the chosen scheduling algorithm. Quit if ^C pressed
    while True:
        if button_count:
            try:
                cotask.task_list.pri_sched()
            except KeyboardInterrupt:
                motor1.set_duty_cycle(0)
#                 print("motor 1 shut off")
                motor2.set_duty_cycle(0)
#                 print("motor 2 shut off")
                break

    # Print a table of task data and a table of shared information data
    print('\n' + str (cotask.task_list))
    print(task_share.show_all())
    print(task1.get_trace())
    print('')

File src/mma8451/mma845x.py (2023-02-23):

"""!
@file mma845x.py
This file contains a @b partly @b written MicroPython driver for the MMA8451 
and MMA8452 accelerometers. It is intended to be used as a starting point for
an exercise in a mechatronics course. 
@author JR Ridgely
@copyright GPL Version 3.0
"""

import micropython
import pyb

## The register address of the STATUS register in the MMA845x
STATUS_REG = micropython.const (0x00)

## The register address of the OUT_X_MSB register in the MMA845x
OUT_X_MSB = micropython.const (0x01)

## The register address of the OUT_X_LSB register in the MMA845x
OUT_X_LSB = micropython.const (0x02)

## The register address of the OUT_Y_MSB register in the MMA845x
OUT_Y_MSB = micropython.const (0x03)

## The register address of the OUT_Y_LSB register in the MMA845x
OUT_Y_LSB = micropython.const (0x04)

## The register address of the OUT_Z_MSB register in the MMA845x
OUT_Z_MSB = micropython.const (0x05)

## The register address of the OUT_Z_LSB register in the MMA845x
OUT_Z_LSB = micropython.const (0x06)

## The register address of the WHO_AM_I register in the MMA845x
WHO_AM_I = micropython.const (0x0D)

## The register address of the DATA_CFG_REG register in the MMA845x which is
#  used to set the measurement range to +/-2g, +/-4g, or +/-8g
XYZ_DATA_CFG = micropython.const (0x0E)

## The register address of the CTRL_REG1 register in the MMA845x
CTRL_REG1 = micropython.const (0x2A)

## The register address of the CTRL_REG2 register in the MMA845x
CTRL_REG2 = micropython.const (0x2B)

## The register address of the CTRL_REG3 register in the MMA845x
CTRL_REG3 = micropython.const (0x2C)

## The register address of the CTRL_REG4 register in the MMA845x
CTRL_REG4 = micropython.const (0x2D)

## The register address of the CTRL_REG5 register in the MMA845x
CTRL_REG5 = micropython.const (0x2E)

## Constant which sets acceleration measurement range to +/-2g
RANGE_2g = micropython.const (0)

## Constant which sets acceleration measurement range to +/-2g
RANGE_4g = micropython.const (1)

## Constant which sets acceleration measurement range to +/-2g
RANGE_8g = micropython.const (2)


class MMA845x:
    """! This class implements a simple driver for MMA8451 and MMA8452
    accelerometers. These inexpensive phone accelerometers talk to the CPU 
    over I<sup>2</sup>C. Only basic functionality is supported: 
    * The device can be switched from standby mode to active mode and back
    * Readings from all three axes can be taken in A/D bits or in g's
    * The range can be set to +/-2g, +/-4g, or +/-8g
    There are many other functions supported by the accelerometers which could 
    be added by someone with too much time on her or his hands :P 
    
    An example of how to use this driver:
    @code
    mma = mma845x.MMA845x (pyb.I2C (1, pyb.I2C.MASTER, baudrate = 100000), 29)
    mma.active ()
    mma.get_accels ()
    @endcode 
    The example code works for an MMA8452 on a SparkFun<sup>TM</sup> breakout
    board. """

    def __init__ (self, i2c, address, accel_range = 0):
        """! Initialize an MMA845x driver on the given I<sup>2</sup>C bus. The 
        I<sup>2</sup>C bus object must have already been initialized, as we're
        going to use it to get the accelerometer's WHO_AM_I code right away. 
        @param i2c An I<sup>2</sup>C bus already set up in MicroPython
        @param address The address of the accelerometer on the I<sup>2</sup>C
            bus 
        @param accel_range The range of accelerations to measure; it must be
            either @c RANGE_2g, @c RANGE_4g, or @c RANGE_8g (default: 2g)
        """

        ## The I2C driver which was created by the code which called this
        self.i2c = i2c

        ## The I2C address at which the accelerometer is located
        self.addr = address

        # Request the WHO_AM_I device ID byte from the accelerometer
        self._dev_id = ord (i2c.mem_read (1, address, WHO_AM_I))

        # The WHO_AM_I codes from MMA8451Q's and MMA8452Q's are recognized
        if self._dev_id == 0x1A or self._dev_id == 0x2A:
            self._works = True
        else:
            self._works = False
            raise ValueError ('Unknown accelerometer device ID ' 
                + str (self._dev_id) + ' at I2C address ' + address)

        # Ensure the accelerometer is in standby mode so we can configure it
        self.standby ()

        # Set the acceleration range to the given one if it's legal
        # self.set_range (accel_range)


    def active (self):
        """! Put the MMA845x into active mode so that it takes data. In active
        mode, the accelerometer's settings can't be messed with. Active mode
        is set by setting the @c ACTIVE bit in register @c CTRL_REG1 to one.
        """

        if self._works:
            reg1 = ord (self.i2c.mem_read (1, self.addr, CTRL_REG1))
            reg1 |= 0x01
            self.i2c.mem_write (chr (reg1), self.addr, CTRL_REG1)


    def standby (self):
        """! Put the MMA845x into standby mode so its settings can be changed.
        No data will be taken in standby mode, so before measurements are to
        be made, one must call @c active(). """

        if self._works:
            reg1 = ord (self.i2c.mem_read (1, self.addr, CTRL_REG1))
            reg1 &= ~0x01
            self.i2c.mem_write(chr(reg1 & 0xFF), self.addr, CTRL_REG1)


    def get_ax_bits (self):
        """! Get the X acceleration from the accelerometer in A/D bits and 
        return it.
        @return The measured X acceleration in A/D conversion bits """

        if self._works:
            x_msb = self.i2c.mem_read(1, self.addr, OUT_X_MSB)
            x_lsb = self.i2c.mem_read(1, self.addr, OUT_X_LSB)        
            return x_msb + x_lsb


    def get_ay_bits (self):
        """! Get the Y acceleration from the accelerometer in A/D bits and 
        return it.
        @return The measured Y acceleration in A/D conversion bits """

        if self._works:
            y_msb = self.i2c.mem_read(1, self.addr, OUT_Y_MSB)
            y_lsb = self.i2c.mem_read(1, self.addr, OUT_Y_LSB)        
            return y_msb + y_lsb


    def get_az_bits (self):
        """! Get the Z acceleration from the accelerometer in A/D bits and 
        return it.
        @return The measured Z acceleration in A/D conversion bits """

        if self._works:
            z_msb = self.i2c.mem_read(1, self.addr, OUT_Z_MSB)
            z_lsb = self.i2c.mem_read(1, self.addr, OUT_Z_LSB)        
            return z_msb + z_lsb


    def get_ax (self):
        """! Get the X acceleration from the accelerometer in g's, assuming
        that the accelerometer was correctly calibrated at the factory.
        @return The measured X acceleration in g's """
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

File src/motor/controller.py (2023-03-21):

"""!
@file controller.py
    This file contains a Controller class which is used for controlling the
    position of a motor using an encoder and a motor driver.

@author Ben Elkayam
@author Roey Mevorach
@author Ermias Yemane

@date   2023-Feb-10
"""
"""
@package pyb                Contains all micro controller tools we use.
@package utime              Contains tools for working with time-related operations.
@package encoder_reader     Contains our encoder driver tools and data.
@package motor_driver       Contains our motor driver tools and interfaces with the encoder.
"""
import pyb, utime
from pyb import Pin as Pin
from motor.encoder_reader import Encoder
from motor.motor_driver import MotorDriver


class Controller:
    """!
    @brief      A control system for positioning a motor using feedback from an encoder and a motor driver.
    @details    The Controller class implements a control loop that uses an Encoder object to get feedback
                on the position of a motor and a MotorDriver object to control the motor. It has methods
                for setting the target position and the proportional gain of the control loop, as well as a
                method for running the control loop and updating the motor's position.
    """

    def __init__(self, kp, setpoint, motor, encoder):
        """!
        @brief      Create a controller object.
        @details    The constructor method initializes the Controller object with the given proportional gain kp,
                    target position setpoint, MotorDriver object motor, and Encoder object encoder. It also initializes
                    the motor_data attribute as a tuple of (0,0), the time attribute as the current time in milliseconds,
                    and prints a message indicating that the Controller object has been created with the given kp and setpoint.
        @param      self The object itself
        @param      kp Proportional gain
        @param      setpoint Target position for the motor
        @param      motor MotorDriver object
        @param      encoder Encoder object
        @return     None
        """
        self.kp = kp
        self.setpoint = setpoint
        self.motor = motor
        self.encoder = encoder
        self.motor_data = (0,0)
        self.time = utime.ticks_ms()
        print(f"Creating controller with KP {self.kp} and setpoint {self.setpoint}")

    def run(self):
        """!
        @brief      Runs the controller.
        @details    Reads the encoder position, calculates the control output using a proportional control law,
                    and sets the duty cycle of the motor. The method also updates the motor data and returns
                    a flag indicating if the motor data has been updated.
        @param      self The object itself
        @return     A flag indicating if the motor data has been updated (0 or 1).
        """
        ##Debugging flag
        flag = 0
        ## Time difference from which the motor runs its controller processes 
        delta_time = utime.ticks_ms() - self.time
        
        #Loop handles motor updating its controller information
        if delta_time >= 10:
            self.encoder.read()
            ## Is the value sent to the motor driver after being scaled by Kp
            output = self.kp * (self.setpoint - self.encoder.position)
            self.motor.set_duty_cycle(output)
            
            self.time = utime.ticks_ms()
            self.motor_data = (delta_time + self.motor_data[0], self.encoder.position)
            flag = 1
        
        return flag

    def set_setpoint(self, setpoint):
        """!
        @brief      Method to set the target position for the motor.
        @details    This method takes in a setpoint parameter and updates the target position of the motor.
        @param      self The object itself
        @param      setpoint Target position for the motor
        @return     None
        """
        self.setpoint = setpoint

    def set_kp(self, kp):
        """!
        @brief      Set the proportional gain.
        @details    This method updates the proportional gain of the controller.
        @param      self The object itself
        @param      kp Proportional gain
        @return     None
        """
        self.kp = kp

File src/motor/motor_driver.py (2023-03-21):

"""!
@file motor_driver.py
    This file contains an MotorDriver class which is used to control a motor using the Pyboard and its pins.

@author Ben Elkayam
@author Roey Mevorach
@author Ermias Yemane

@date   2023-Feb-10
"""
"""!
@package pyb                Contains all micro controller tools we use.
"""
import pyb
from pyb import Pin as Pin

# Yellow (channel A) leads for clockwise
# Blue (channel B) leads for clockwise

class MotorDriver:
    """!
    @brief      This class is used to control a motor using the Pyboard and its pins.
    @details    The class initializes the pins for the enable, input 1, and input 2 pins of the motor.
                It also initializes a timer for PWM control of the motor. The class provides a function
                to set the duty cycle of the PWM signal applied to the motor to control its speed.
    """

    def __init__ (self, en_pin, in1pin, in2pin, timer_num):
        """!
        @brief      Constructor method for MotorDriver class
        @details    The constructor method initializes a MotorDriver object with the given enable pin (en_pin), 
                    input 1 pin (in1pin), input 2 pin (in2pin), and timer number (timer_num). It sets the specified 
                    pins as outputs, creates a timer using the given timer number, and initializes the pin_en, 
                    ch1, and ch2 attributes.
        @param      self The object itself
        @param      en_pin Pin number for the enable pin
        @param      in1pin Pin number for the input 1 pin
        @param      in2pin Pin number for the input 2 pin
        @param      timer_num Timer number
        @return     None
        """
        ## Sets up the in1pin for the motor to be push-pull
        pin1 = Pin(in1pin, Pin.OUT_PP)
        ## Sets up the in2pin for the motor to be push-pull
        pin2 = Pin(in2pin, Pin.OUT_PP)
        ## Creates the timer which will run the motor
        timer = pyb.Timer(timer_num, freq=0x4E20)
        self.pin_en = Pin(en_pin, Pin.OUT_OD, Pin.PULL_UP)
        self.ch1 = timer.channel(1, pyb.Timer.PWM, pin=pin1)
        self.ch2 = timer.channel(2, pyb.Timer.PWM, pin=pin2)
        print("Creating a motor driver")

    def set_duty_cycle (self, level):
        """!
        @brief      This method sets the duty cycle of the PWM signal that drives the motor.
        @details    The duty cycle is set based on the level parameter. If the level is negative, the duty cycle of
                    the PWM signal to channel 1 of the motor is set to -1 times the level, and the duty cycle of the
                    PWM signal to channel 2 of the motor is set to 0. If the level is positive, the duty cycle of the
                    PWM signal to channel 1 of the motor is set to 0, and the duty cycle of the PWM signal to channel
                    2 of the motor is set to the level. If the level is 0, the duty cycle of both channels is set to 0.
        @param      self The object itself
        @param      level The duty cycle of the PWM signal as a percentage (-100 to 100).
        @return     None
        """
        self.pin_en.value(1)

        if level < 0:
            self.ch1.pulse_width_percent(-1 * level)
            self.ch2.pulse_width_percent(0)
        elif level > 0:
            self.ch1.pulse_width_percent(0)
            self.ch2.pulse_width_percent(level)
        else:
            self.ch1.pulse_width_percent(0)
            self.ch2.pulse_width_percent(0)
            
#         print (f"Setting duty cycle to {level}")

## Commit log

2023-02-21 thermal camera datasheet
2023-02-21 solidworksv1
    parts
    [Part2.SLDPRT, bearings.SLDPRT]
2023-02-28 Semi-Finalized CAD Model
    Contains all but one parts and all the parts contained are finalized
    [3d topbase.SLDPRT, 3d topbase.STL, 3d topbaseV2.STL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]
2023-03-07 Final CAD
    [Mainassemb.SLDASM, clamp1.SLDPRT, clamp1.STL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]
2023-03-09 testing motors
2023-03-09 added user input for kp and setpoint for motors
2023-03-09 pitch and yaw
    has both motors kp and setpoint values
2023-03-09 modified SLDWRK
    [3d topbase.SLDPRT, 57545K633_Steel Worm.SLDPRT, 57545K764_Metal Worm Gear.SLDPRT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]
2023-03-09 CAD edit for winch
    winch edit
    [57545K633_Steel Worm.SLDPRT, 57545K764_Metal Worm Gear.SLDPRT, winchmount.SLDPRT]
2023-03-11 SLDWRK update
    [57545K633_Steel Worm.STL, 57545K764_Metal Worm Gear.STL, Part1.STL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]
2023-03-13 find_hotspot works & pitch and yaw motors working together
2023-03-14 Fixed motor 180 deg turn and added math for targetting
    [test_main.py]
2023-03-14 Finalized Calibration
    we done
2023-03-21 cleaned up git
    [3d topbase.SLDPRT, 57545K633_Steel Worm.SLDPRT, 57545K764_Metal Worm Gear.SLDPRT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]
